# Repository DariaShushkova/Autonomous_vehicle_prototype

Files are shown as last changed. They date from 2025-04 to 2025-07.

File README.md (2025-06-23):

<div align="center">

Typing SVG (https://git.io/typing-svg)

Autonomous Driving System (**ADS**) is a **Line Following and Obstacle Avoiding Robot** built as semester project for **System Engineering & Prototyping** module at Hochschule Hamm-Lippstadt.

</div>

### Project Structure

1. Software For ADS
    - Directory: Autonomous Vehicle Code/
    - Contents: CodeOfTheSystem/, README.md
    - [Documenation](https://github.com/DariaShushkova/Autonomous_vehicle_prototype/tree/main/Autonomous%20Vehicle%20Code)

2. Datasheets for all Components
    - Directory: Hardware Datasheets/
    - Contents: Datasheets, README.md
    - [Documentation](https://github.com/DariaShushkova/Autonomous_vehicle_prototype/tree/main/Hardware%20Datasheets)

3. Mechanical Prototypes
    - Directory: Mechanical Prototype Design/
    - Contents: SolidWorks Parts, STL files for 3D printing, README.md
    - [Documentation](https://github.com/DariaShushkova/Autonomous_vehicle_prototype/tree/main/Mechanical%20Prototype%20Design)

4. Analysis and Visual Representation
    - Directory: Prototype Analysis/
    - Contents: Code Representation/, Visualization/
    - [Documentation](https://github.com/DariaShushkova/Autonomous_vehicle_prototype/tree/main/Prototype%20Analysis)

5. Simulated Circuitry
    - Directory: Simulation/
    - Contents: ArduinoCodeForDeployment/, Circuit Diagram & Setup
    - [Documenation](https://github.com/DariaShushkova/Autonomous_vehicle_prototype/tree/main/simulation)

6. Corrent and Voltage Measurement
    - Directory: CurrentAndVoltageMeasurement/
    - Contents: Images of voltage and current measurements for all components.
    - [Documentation](https://github.com/DariaShushkova/Autonomous_vehicle_prototype/tree/main/CurrentAndVoltageMeasurements)

7. Unit Testing
    - Directory: Software Testing
    - Contents: Unit_Tests/, all program files, Voltage Measurement Protocol.pdf
    - [Documentation](https://github.com/DariaShushkova/Autonomous_vehicle_prototype/tree/main/Software%20Testing)

### Competiton Recording
[Youtube](https://youtu.be/u-iqNwPsLXI)

### Components

1. chassis
2. DC Motors x2
3. IR Sensor x2
4. Ultrasonic Sensor x2
5. Motor Driver
6. Wheels
7. Color Sensor
8. Battery
9. Breadboard
10. Arduino

### Contributors

- [Daria Shushkova](https://github.com/DariaShushkova)
- [Andrey Sysoev](https://github.com/andrey-sysoev)
- [Mohamed Amer](https://github.com/amer195)
- [SamRB-dev](https://github.com/SamRB-dev)

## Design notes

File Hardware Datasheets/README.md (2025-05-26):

<div align="center">

Typing SVG (https://git.io/typing-svg)

</div>

### Overview

This directory contains the datasheets for every components used in the project.

### File Included

- Arduino Uno R4.pdf
- Color Sensor TCS3200.pdf
- Conrad LiPo Battery 3200mAh.pdf
- KY-033 IR Sensor.pdf
- Motor Driver L298N.pdf
- Ultrasonic Sensor HCSR04.pdf

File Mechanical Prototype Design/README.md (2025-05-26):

<div align="center">

Typing SVG (https://git.io/typing-svg)

</div>

### Overview

This part of the project contains 3D models for an Arduino-based autonomous vehicle prototype that will be used on the deployment stage.

### Directory Included

- [SolidWorks Parts](https://github.com/DariaShushkova/Autonomous_vehicle_prototype/tree/main/Mechanical%20Prototype%20Design/SolidWorks%20Parts) (Design files)
- [STL files](https://github.com/DariaShushkova/Autonomous_vehicle_prototype/tree/main/Mechanical%20Prototype%20Design/STL%20files) (For 3D printing)

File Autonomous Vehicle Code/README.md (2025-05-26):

<div align="center">

Typing SVG (https://git.io/typing-svg)

</div>

### Overview

This directory contains the code for the robot. The code consists of Motor control, robot navigation and ultrasonic sensor component. The motor control component (**MotorControl.h & MotorControl.cpp**) handles the states such as *leftSpeed, rightSpeed, leftForward, leftBackward, rightForward, rightBackward* and movement to different directions. The navigation component (**RobotNavigation.cpp & RobotNavigation.h**) handles obstacle detection, avoidance and movement based on the states of Motor controller. And lastly, the ultrasonic component (**UltrasonicSensor.h & UltrasonicSensor.cpp**) contains the code for ultrasonic sensor.

### File Included

1. Header Files
    - MotorControl.h
    - RobotNavigation.h
    - UltrasonicSensor.h
2. Program files
    - main.cpp
    - RobotNavigation.cpp
    - UltrasonicSenor.cpp

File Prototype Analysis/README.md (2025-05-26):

<div align="center">

Typing SVG (https://git.io/typing-svg)

</div>

### Overview

This directory contains the prototype analysis report in the form of code and visualization. The visualization contains the jpg files for various diagrams and the code contains html representation of the diagrams drawn in [Draw.io](https://draw.io).

### Directory Included

- [Code Representation](https://github.com/DariaShushkova/Autonomous_vehicle_prototype/tree/main/Prototype%20Analysis/Code%20Representation)
- [Visualization](https://github.com/DariaShushkova/Autonomous_vehicle_prototype/tree/main/Prototype%20Analysis/Visualization)

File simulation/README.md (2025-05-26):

<div align="center">

Typing SVG (https://git.io/typing-svg)

</div>

### Overview

This part of the project implements an Arduino-based autonomous vehicle prototype. The vehicle uses line detection and obstacle avoidance, including color-based object handling, to navigate predefined tracks. Supports routing variations like ovals, figure-eights, and parking maneuvers. Also contains the deployed code for the robot.

### Features

- Line tracking
- Obstacle detection and avoidance
- Color-based decision logic
- Speed optimization
- Supports various driving patterns (oval, figure-eight, parking)

### Simulation

The project is modeled and tested using Tinkercad.

[View Simulation](https://www.tinkercad.com/things/jz61uT7Gl9G-autonomous-vehicle-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)

### Files & Directory Included

- [ArduinoCodeForDeployment](https://github.com/DariaShushkova/Autonomous_vehicle_prototype/tree/main/simulation/ArduinoCodeForDeployment)
- AutonomousVehicleCode.cpp
- Circuit Diagram.pdf
- CircuitSetup.jpg

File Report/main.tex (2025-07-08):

\documentclass[conference]{IEEEtran}
\IEEEoverridecommandlockouts
\usepackage{comment}
\usepackage{cite}
\usepackage{amsmath,amssymb,amsfonts}
\usepackage{algorithmic}
\usepackage{graphicx}
\usepackage{textcomp}
\usepackage{xcolor}
\usepackage{hyperref}
\usepackage{listings}
\usepackage{float}
\usepackage{graphicx}
\usepackage{adjustbox}
\usepackage{enumitem}
\lstset{
  language=C++,
  basicstyle=\ttfamily\footnotesize,
  keywordstyle=\color{blue},
  commentstyle=\color{gray}\itshape,
  stringstyle=\color{red},
  numbers=none,
  numbersep=5pt,
  frame=single,
  breaklines=true,
  breakatwhitespace=true,
  postbreak=\mbox{\textcolor{gray}{$\hookrightarrow$}\space},
  showstringspaces=false,
  captionpos=b,
  tabsize=2
}

\def\BibTeX{{\rm B\kern-.05em{\sc i\kern-.025em b}\kern-.08em
    T\kern-.1667em\lower.7ex\hbox{E}\kern-.125emX}}

\begin{document}

\title{Design and Implementation of a Line Following and Obstacle Avoidance Robot}

\author{
\IEEEauthorblockN{Mohamed Amer\IEEEauthorrefmark{1}, Daria Shushkova\IEEEauthorrefmark{1},Andrey Sysoev\IEEEauthorrefmark{1}, Sadim Rahman\IEEEauthorrefmark{1}}
\IEEEauthorblockA{\IEEEauthorrefmark{1}Systems Engineering and Prototyping, BSc Electronic Engineering\\
Hochschule Hamm-Lippstadt, Lippstadt, Germany\\
\{mohamed-ahmed-mohamed-ali.amer, daria.shushkova, andrey.sysoev, sadim-rahman.badhan\}@stud.hshl.de}
}

\maketitle

%\begin{abstract}
%This paper presents the.
%\end{abstract}

%\begin{IEEEkeywords}
%Line follower robot,
%\end{IEEEkeywords}

\section{Introduction}
This project focuses on the development of a simple mobile robot that can autonomously follow a black line on a white surface and avoid obstacles placed in its path. The robot uses infrared sensors to detect the line and an ultrasonic sensor to detect nearby objects. An Arduino microcontroller is used to process sensor inputs and control motors accordingly.

\section{System Design and Engineering}
The robot design was developed based on \textbf{tasks} and \textbf{milestones} defined at the beginning of the project. These included line following, obstacle detection and avoidance, and integration of all components into a working prototype. It uses two infrared (IR) sensors to detect the black line and an ultrasonic sensor to measure the distance from obstacles. These sensors send signals to an Arduino Uno, that acts as the main controller.

The Arduino processes data and decides how the system should respond: either adjusting its path to stay on the line or stopping and maneuvering around an obstacle. Movement is handled by two DC motors controlled through an L298N motor driver.

Power is provided by a 9V battery pack, with regulation to supply the required voltages for the microcontroller and sensors. A simplified block diagram of the system is shown in Fig.~\ref{fig:block}

The vision of a system started with creating SysML diagrams to preserve and structure our project. It has the four Pillars of SysML:
\vspace{1em}
\begin{itemize}
  \item Requirements modeling (e.g., requirement diagram)
  \item Parametric modeling
  \item Structural modeling (e.g., Block Definition diagrams (BDD), Internal Block diagrams (IBD))
  \item Behavioral modeling (e.g., Use Case diagrams, Activity Diagrams, Sequence Diagrams, State Machine Diagrams)
\end{itemize}
\vspace{1em}
\begin{enumerate}

\item \textbf{Requirement Diagram}

 \hspace*{1em}It contains both \textbf{functional} and \textbf{nonfunctional} requirements of the autonomous vehicle system. These include navigation, obstacle handling, speed optimization, and route management,  with their derived requirements and hardware components.
 
 \hspace*{1em}See Fig~\ref{fig:req} the Requirement diagram.
 \vspace{1em}
\item \textbf{Parametric Diagram}

 \hspace*{1em}The \textbf{ Parametric Diagram} define parametric relationships between properties of blocks. This section uses parametric diagrams to represent mathematical and physical constraints of system behavior. See  Fig~\ref{fig:par} the Parametric diagram.
\vspace{1em}
\item \textbf{Block Definition Diagram}

\hspace*{1em}The \textbf{Block Definition Diagram (BDD)} provides a  structural decomposition of the \textit{Autonomous Vehicle System}. It represents the main logical blocks and how they are hierarchically related through composition relationships.

\vspace{1em}The  system is broken down into three primary subsystems:
\begin{itemize}
    \item \textbf{Chassis:} Includes physical mounting blocks such as the battery and breadboard holder, IR sensor holder, motor holder, and ultrasonic sensor holder.
    
    \item \textbf{Controllers:} Main controller (\textit{Arduino}) and the motor controller block responsible for driving the actuators.
    
    \item \textbf{Components:} Wheels and motors, which are part of the physical actuation system.
\end{itemize}
\hspace*{1em}See  Fig~\ref{fig:blockDef} the Block Definition diagram .

\item\textbf{Use Case Diagram}

Use case diagram models the interactions between \textbf{User} (the operator) and system functionalities. 
The diagram focuses on a \textit{"happy path"} — \textbf{Drive Autonomously}, which includes supporting behaviors like:

\begin{itemize}[nosep, left=0pt]
    \item Adjust Speed
    \item Avoid Obstacle
    \item Follow Path
\end{itemize}
\vspace{0.8em}
Extra behaviors such as \textbf{Drive in Oval} and \textbf{Drive in Figure Eight} are modeled as extensions of the routing logic.

\hspace*{1em}See  Fig~\ref{fig:use} the Use Case diagram.
\vspace{1em}
\item \textbf{State Machine Diagram}

The system begins in the "\textbf{stopped}" state. Upon initialization,it switches to the "\textbf{perform autonomous navigation}" state, where it drives left or right based on the input of the line-following sensor. If obstacle has been detected, system transitions to the "\textbf{obstacle\_avoid}" state. 
\hspace*{1em}In "\textbf{obstacle\_avoid}", the vehicle maneuvers around the obstacle:
\begin{itemize}
    \item it goes "\textbf{backward}" until save distance to do a maneuver
    \item chooses path depending if where are walls on the "\textbf{left}" or "\textbf{right}"
    \item  does "\textbf{line search}" to find the path after obstacle avoidance have been completed
\end{itemize}
\hspace*{1em}See  Fig~\ref{fig:state machine-diagram} the State Machine diagram.
\vspace{1em}
\item \textbf{Sequence Diagram}

\hspace*{1em}The \textbf{Sequence Diagram} shows the interaction between the Operator, AVS Controller, sensors, and motor control during autonomous navigation. The controller continuously uses path and obstacle data to send commands to motors: \texttt{setForward()}, \texttt{setLeft()}, or \texttt{setRight()}.

\hspace*{1em}If an obstacle is detected, the system enters \textbf{Obstacle Avoid Mode}, executing timed motor actions. An \texttt{alt} block handles conditional stopping or recovery based on search timeout and sensor feedback.

\hspace*{1em}See  Fig~\ref{fig:seq} the Sequence diagram.
\end{enumerate}
\vspace{1em}
\section{Prototyping and Design}
Our team was supplied with several Electronic components and a pre-designed chassis for development of the line follower vehicle. Our team was tasked to design a suitable mechanical design that would perform well in practice while utilizing all of the functionalities requested. A iterative design methodology was used to reach the final design made. 
\subsection{Electronic Components}
As shown in Table~\ref{tab:Electronic Components} a brief about the electronic components supplied and their purpose is mentioned. Key components that needed much attention were the infrared sensor, the battery and the motor driver. The Infrared sensor was a digital active high sensor.Thus, it was needed to be calibrated on the line we are following. Furthermore, dealing with the battery and the motor driver supplied, it was critical to ensure that voltages coming out of the motor driver voltage regulator are 5 volts. otherwise, this will expose the components to permanent damage. For safety purposes and avoiding any damaging to the components, we simulated the entire circuit in TinkerCad \cite{tinkercad}.

\subsection{Virtual and Physical Prototypes}
All of the prototyping design iterations were simulated in Solid works software. Our goal was to design as few parts as we can to avoid the given printing time limit. It was agreed on at the end to use the following parts followed by their main objective: \begin{itemize}
    \item \textbf{2x Motor mounts:} The motor mounts were used to mount the motors in a rigid way so it can support the entire weight of the vehicle.
     \item \textbf{2x IR sensor mounts:} The main objective is to keep the IR sensors too close to the ground to avoid lighting noise from the surrounding environment
      \item \textbf{2x Ultrasonic mounts:} Really lightweight components just to fix the ultrasonic without causing a high penality in printing time
       \item \textbf{battery and breadboard mount:} It function is to be multifunctional part holding the breadboard on its upper side and securing the battery underneath it
\end{itemize} 
Our first print trial was not so successful at the beginning due to unaccounted error in our design. Then the parts were modified to have some fit tolerance to account for the error resulting from the 3D printer. Moreover on design iterations, we included slots instead of holes for the IR sensors so their position can be easily modified if needed. A visualization of the final prototype reached is shown in Figure~\ref{fig:prototype}.
\begin{figure}[H]
    \centering
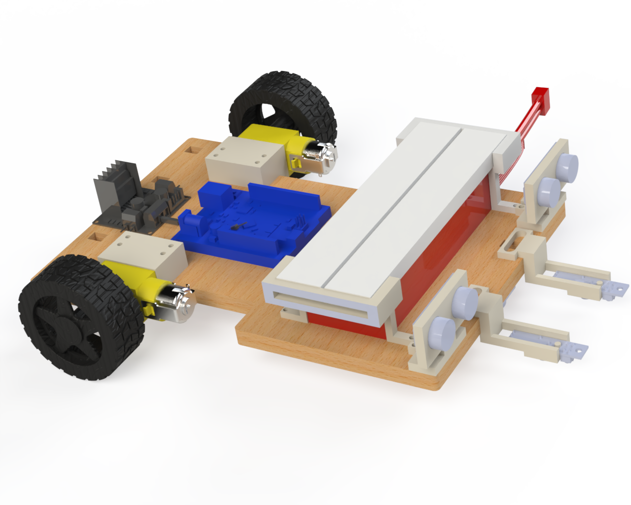
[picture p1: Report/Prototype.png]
    
    \caption{Block diagram of the line following and obstacle avoidance robot.}
    \label{fig:prototype}
\end{figure}

\subsection{Hardware Assembly}
All components were mounted on a chassis and connected as per the schematic. For assembly, all of the parts were mounted using spax screws in 3 different lengths : 10mm, 16mm, 20mm with all of them being M3 diameter. Some holes in the wooden chassis were done using a drill. All of the components were mounted without any adhesive materials. In our assembly, it was made sure that all components were firmly secured in position. 

\section{Circuit Design}
%\begin{itemize}
 %   \item The schematic includes sensors, motor driver, Arduino, and power source.
  %  \item Wiring includes proper voltage connections and pin mappings for sensors and motors.
%\end{itemize}

The autonomous vehicle circuit integrates multiple sensor and actuator subsystems using an Arduino Uno as the main controller. The complete circuit layout simulation in tinkercad is shown in Fig.~\ref{fig:CircuitSetup}.

The wiring was designed to fulfill three key goals: modularity, robustness, and safe power distribution. Each subsystem was treated as an independent module, allowing for easier debugging and incremental development.

\subsection{Sensor Integration}
\begin{itemize}
  \item \textbf{Infrared Line Sensors (2x)} are connected to digital input pins D12 and D13. These sensors detect the black line against the white surface, and their values are read in real-time to determine the robot's lateral alignment.

  \item \textbf{Ultrasonic Sensors (2x)} are mounted on the front-left and front-right sides. Their trigger and echo pins are connected to D6/D7 (right) and D8/D9 (left). These provide real-time distance feedback to avoid collisions.

  \item \textbf{Color Sensor (1x)} is connected to analog pins A0 to A4. It adds redundancy to object classification, allowing the robot to treat red-colored obstacles differently (e.g., push or bypass).
\end{itemize}

\subsection{Actuator Wiring}
The circuit schematic of the Motor Driver along with the motors and ultrasonic sensors is shown in ~\ref{fig:Schematic}.
\begin{itemize}
  \item \textbf{Motor Driver (L298N)} is used to control two DC motors. It is connected to:
  \begin{itemize}
    \item PWM pins D10 and D11 for speed control
    \item Direction control pins D2–D5
  \end{itemize}
  The motors are powered directly from the 12V battery pack via the motor driver's onboard regulator.
\end{itemize}

\subsection{Power Management}
\begin{itemize}
  \item A 12V DC battery pack supplies power to both motors and the Arduino.
  \item A voltage regulator onboard the L298N downscales the 12V to 5V for the Arduino and sensors, avoiding voltage spikes and protecting delicate components.
  \item Decoupling capacitors are placed across power lines to minimize electrical noise and ensure stable analog sensor readings.
\end{itemize}

\subsection{Pin Mapping Overview}
The Table ~\ref{tab:pinmap} shows the pins that were used in details.
\begin{table}[H]
\centering
\caption{Key Pin Assignments}
\label{tab:pinmap}
\begin{tabular}{|l|l|}
\hline
\textbf{Component} & \textbf{Pin(s)} \\ \hline
IR Sensor (Left) & D13 \\ \hline
IR Sensor (Right) & D12 \\ \hline
Ultrasonic Sensor (Left) & D8 (Trig), D9 (Echo) \\ \hline
Ultrasonic Sensor (Right) & D6 (Trig), D7 (Echo) \\ \hline
Left Motor & D2 (F), D3 (B), D10 (PWM) \\ \hline
Right Motor & D4 (F), D5 (B), D11 (PWM) \\ \hline
Color Sensor & A0–A4 \\ \hline
\end{tabular}
\end{table}

\subsection{Schematic Analysis}
The circuit was simulated and verified using Tinkercad and real-world breadboard prototyping. Care was taken to route ground lines properly, avoid floating inputs, and apply pull-down resistors where needed.

The design emphasizes modularity, with all sensors and motors detachable via male/female header connectors for ease of maintenance and reassembly.

\section{Software Implementation}
\label{soft}

\subsection{Initialization of Sensors and Actuators}
\subsubsection*{\textbf{1. Sensors Initialization}}

\begin{enumerate}[label=\alph*)]

\item \textbf{Ultrasonic Sensors (Left/Right)} — Pins for the ultrasonic sensors are defined in the file 'UltrasonicSensor.h'. They are set up and initialized in the 'UltrasonicSensor.cpp' and 'main.cpp' files. Relevant snippets are shown below:

\begin{lstlisting}[language=C++, caption=Pin definitions in UltrasonicSensor.h]
// Ultrasonic sensor pin definitions
#define LEFT_TRIG_PIN 8
#define LEFT_ECHO_PIN 9
#define RIGHT_TRIG_PIN 6
#define RIGHT_ECHO_PIN 7
\end{lstlisting}

\begin{lstlisting}[language=C++, caption=Pin setup in UltrasonicSensor.cpp]
// Set trigger as output and echo as input
void UltrasonicSensor::begin() {
   pinMode(trigPin, OUTPUT);
   pinMode(echoPin, INPUT);
}
\end{lstlisting}

\begin{lstlisting}[language=C++, caption=Sensor initialization in main.cpp]
// Create hardware instances
...
UltrasonicSensor rightUltrasonic(
  RIGHT_TRIG_PIN,
  RIGHT_ECHO_PIN);
UltrasonicSensor leftUltrasonic(
  LEFT_TRIG_PIN,
  LEFT_ECHO_PIN);
RobotNavigation robotNav(
  &rightUltrasonic,
  &leftUltrasonic,
  &motor);
 
// Initialize ultrasonic sensors
void setup() {
   ...
   rightUltrasonic.begin();
   leftUltrasonic.begin();
   ...
}
\end{lstlisting}

\item \textbf{IR Sensors (Left/Right)} — Pins for the IR sensors are defined in 'RobotNavigation.h' and initialized in 'RobotNavigation.cpp' and in 'main.cpp'. Relevant snippets are shown below:

\begin{lstlisting}[language=C++, caption=IR sensor pin definitions in RobotNavigation.h]
// Line sensor digital pins
#define LINE_SENSOR_LEFT 13
#define LINE_SENSOR_RIGHT 12
\end{lstlisting}

\begin{lstlisting}[language=C++, caption=IR sensor pin initialization in RobotNavigation.cpp]
void RobotNavigation::begin() {
  pinMode(LINE_SENSOR_LEFT, INPUT);
  pinMode(LINE_SENSOR_RIGHT, INPUT);
}
\end{lstlisting}

\begin{lstlisting}[language=C++, caption=IR sensor pin initialization in main.cpp]
void setup() {
  ...
  // Start navigation system
  robotNav.begin();
}
\end{lstlisting}

\item \textbf{Color Sensor} — Pins for the color sensor are defined in 'ColorSensor.h' and initialized in 'ColorSensor.cpp'. Relevant snippets are shown below:

\begin{lstlisting}[language=C++, caption=Color sensor pin definitions in ColorSensor.h]
// Pin definitions
#define COLOR_SENSOR_OUTPUT_FREQUENCY_INPUT_S0 A0
#define COLOR_SENSOR_OUTPUT_FREQUENCY_INPUT_S1 A1
#define COLOR_SENSOR_PHOTODIODE_INPUT_S2 A2
#define COLOR_SENSOR_PHOTODIODE_INPUT_S3 A3
#define COLOR_SENSOR_OUTPUT_PIN A4
\end{lstlisting}

\begin{lstlisting}[language=C++, caption=Color sensor pin initialization in ColorSensor.cpp]
void ColorSensor::ColorSensorInit() {
    pinMode(
      COLOR_SENSOR_OUTPUT_FREQUENCY_INPUT_S0,
      OUTPUT);
    pinMode(
      COLOR_SENSOR_OUTPUT_FREQUENCY_INPUT_S1,
      OUTPUT);
    pinMode(
      COLOR_SENSOR_PHOTODIODE_INPUT_S2,
      OUTPUT);
    pinMode(
      COLOR_SENSOR_PHOTODIODE_INPUT_S3,
      OUTPUT);
    pinMode(
      COLOR_SENSOR_OUTPUT_PIN,
      INPUT);

    digitalWrite(
      COLOR_SENSOR_OUTPUT_FREQUENCY_INPUT_S0,
      HIGH); // Full scale
    digitalWrite(
      COLOR_SENSOR_OUTPUT_FREQUENCY_INPUT_S1,
      LOW); // Frequency scaling = 20%
}
\end{lstlisting}
\end{enumerate}

\subsubsection*{\textbf{2. Actuators (Motors) Initialization}}
Motor Control Pins are defined in the file 'MotorControl.h'. Their setup and initialization are made in the 'main.cpp' file. Relevant snippets are shown below:

\begin{lstlisting}[language=C++, caption=Pin definitions in MotorControl.h]
// Motor control pin definitions
#define LEFT_MOTOR_SPEED_PIN 10
#define RIGHT_MOTOR_SPEED_PIN 11
#define LEFT_MOTOR_FORWARD_PIN 2
#define LEFT_MOTOR_BACKWARD_PIN 3
#define RIGHT_MOTOR_FORWARD_PIN 4
#define RIGHT_MOTOR_BACKWARD_PIN 5
\end{lstlisting}

\begin{lstlisting}[language=C++, caption=Pins initialization in main.cpp]
// Create hardware instances
MotorControl motor;
...

RobotNavigation robotNav(
  &rightUltrasonic,
  &leftUltrasonic,
  &motor
);
// Arduino initialization
void setup() {
  // Setup motor pins as outputs
  pinMode(LEFT_MOTOR_SPEED_PIN, OUTPUT);
  pinMode(RIGHT_MOTOR_SPEED_PIN, OUTPUT);
  pinMode(LEFT_MOTOR_FORWARD_PIN, OUTPUT);
  pinMode(LEFT_MOTOR_BACKWARD_PIN, OUTPUT);
  pinMode(RIGHT_MOTOR_FORWARD_PIN, OUTPUT);
  pinMode(RIGHT_MOTOR_BACKWARD_PIN, OUTPUT);
  ...
}
\end{lstlisting}

\subsubsection*{Key Initialization Features}
\begin{enumerate}
  \item \textbf{Pin Abstraction}
    \begin{itemize}
      \item Hardware pins are abstracted via \verb|#define| macros.
      \item Logical separation of sensor and actuator types.
    \end{itemize}
  \item \textbf{Modular Initialization}
    \begin{itemize}
      \item Each sensor type has its own initialization routine.
      \item Motor control setup is centralized in \texttt{main.cpp}.
    \end{itemize}
  \item \textbf{Hardware–Software Mapping}
    \begin{itemize}
      \item On Fig.~\ref{fig:block}, the block diagram shows how each hardware component is mapped to specific software-controlled pins in the Arduino controller.
    \end{itemize}
\end{enumerate}

This summary ensures the reader understands the overarching design—pin abstraction, modular setup, mapping, and your carefully ordered startup sequence—before diving into higher‑level behavior logic.

\subsection{Movement Control Algorithms}

\subsubsection*{\textbf{1. Core Movement Methods}}

\begin{enumerate}[label=\alph*)]

\item \textbf{Forward and Backward Motion} - The robot’s linear motion is achieved through symmetric control of both motors using Pulse Width Modulation (PWM) for speed regulation. The direction of rotation is set by toggling the appropriate H-bridge control pins. The methods of the \texttt{MotorControl class} in 'MotorControl.cpp' show the implementation of forward and reverse movement:

\begin{lstlisting}[language=C++, caption=Forward and backward movement functions]
// Move robot straight forward at given speed
void MotorControl::moveForward(int speed) {
  analogWrite(LEFT_MOTOR_SPEED_PIN, speed);
  analogWrite(RIGHT_MOTOR_SPEED_PIN, speed);
  digitalWrite(LEFT_MOTOR_FORWARD_PIN, LOW);
  digitalWrite(LEFT_MOTOR_BACKWARD_PIN, HIGH);
  digitalWrite(RIGHT_MOTOR_FORWARD_PIN, LOW);
  digitalWrite(RIGHT_MOTOR_BACKWARD_PIN, HIGH);
}

// Move robot straight backward at given speed
void MotorControl::moveBackward(int speed) {
  analogWrite(LEFT_MOTOR_SPEED_PIN, speed);
  analogWrite(RIGHT_MOTOR_SPEED_PIN, speed);
  digitalWrite(LEFT_MOTOR_FORWARD_PIN, HIGH);
  digitalWrite(LEFT_MOTOR_BACKWARD_PIN, LOW);
  digitalWrite(RIGHT_MOTOR_FORWARD_PIN, HIGH);
  digitalWrite(RIGHT_MOTOR_BACKWARD_PIN, LOW);
}
\end{lstlisting}

\textbf{Key Algorithm:}
\begin{itemize}
  \item PWM signals regulate motor speed via \verb|analogWrite()|.
  \item H-bridge circuits manage direction through digital pins.
  \item Equal PWM ensures coordinated, straight-line movement.
\end{itemize}

\item \textbf{Pivotal Turning} - For medium-radius turns, one motor is activated while the other is disabled, allowing the robot to pivot around the unpowered wheel. The \verb|turnLeft()| and \verb|turnRight()| methods implement this by powering one motor while setting both control pins for the other motor to \verb|LOW|, causing it to freewheel or coast. This creates a smoother turn compared to a point rotation.

\begin{lstlisting}[language=C++, caption=Single-wheel pivot turn functions]
// Turn robot to the left
void MotorControl::turnLeft(int speed) {
  analogWrite(LEFT_MOTOR_SPEED_PIN, speed);
  digitalWrite(LEFT_MOTOR_FORWARD_PIN, LOW);
  digitalWrite(LEFT_MOTOR_BACKWARD_PIN, HIGH);
  digitalWrite(RIGHT_MOTOR_FORWARD_PIN, LOW);
  digitalWrite(RIGHT_MOTOR_BACKWARD_PIN, LOW);
}

// Turn robot to the right
void MotorControl::turnRight(int speed) {
  analogWrite(RIGHT_MOTOR_SPEED_PIN, speed);
  digitalWrite(LEFT_MOTOR_FORWARD_PIN, LOW);
  digitalWrite(LEFT_MOTOR_BACKWARD_PIN, LOW);
  digitalWrite(RIGHT_MOTOR_FORWARD_PIN, LOW);
  digitalWrite(RIGHT_MOTOR_BACKWARD_PIN, HIGH);
}

\end{lstlisting}

\textbf{Key Algorithm:}
\begin{itemize}
    \item Only one motor is actively powered for the turn.
    \item The other motor is disabled and its wheel is allowed to coast, serving as the pivot point.
    \item The turning radius is determined by the robot's geometry and the speed of the powered wheel.
\end{itemize}

\item \textbf{In-Place Rotation} - In-place rotation is accomplished by driving both motors in opposite directions at equal speed. This results in a zero turning radius, allowing the robot to pivot around its center. The technique is useful in constrained environments or for rapid heading adjustments.

\begin{lstlisting}[language=C++, caption=Counter-rotational in-place turning]
// Rotate robot to the right
void MotorControl::rotateRight(int speed) {
  analogWrite(RIGHT_MOTOR_SPEED_PIN, speed);
  analogWrite(LEFT_MOTOR_SPEED_PIN, speed);
  digitalWrite(LEFT_MOTOR_FORWARD_PIN, HIGH);
  digitalWrite(LEFT_MOTOR_BACKWARD_PIN, LOW);
  digitalWrite(RIGHT_MOTOR_FORWARD_PIN, LOW);
  digitalWrite(RIGHT_MOTOR_BACKWARD_PIN, HIGH);
}

// Rotate robot to the left
void MotorControl::rotateLeft(int speed) {
  analogWrite(RIGHT_MOTOR_SPEED_PIN, speed);
  analogWrite(LEFT_MOTOR_SPEED_PIN, speed);
  digitalWrite(LEFT_MOTOR_FORWARD_PIN, LOW);
  digitalWrite(LEFT_MOTOR_BACKWARD_PIN, HIGH);
  digitalWrite(RIGHT_MOTOR_FORWARD_PIN, HIGH);
  digitalWrite(RIGHT_MOTOR_BACKWARD_PIN, LOW);
}

\end{lstlisting}

\textbf{Key Algorithm:}
\begin{itemize}
  \item Opposite motor directions produce a central rotation.
  \item Equal PWM ensures balanced torque and pivoting.
  \item Enables highly responsive directional changes.
\end{itemize}

\item \textbf{Stopping Mechanism} - To halt motion, both motors are actively short-braked by setting both control lines to \verb|HIGH|. Simultaneously, PWM is set to its maximum to ensure full coil engagement. This braking approach ensures faster and more stable stops compared to passive coasting.

\begin{lstlisting}[language=C++, caption=Active braking mechanism]
// Stop robot
void MotorControl::stopMotors() {
  analogWrite(LEFT_MOTOR_SPEED_PIN, 255);
  analogWrite(RIGHT_MOTOR_SPEED_PIN, 255);
  digitalWrite(LEFT_MOTOR_FORWARD_PIN, HIGH);
  digitalWrite(LEFT_MOTOR_BACKWARD_PIN, HIGH);
  digitalWrite(RIGHT_MOTOR_FORWARD_PIN, HIGH);
  digitalWrite(RIGHT_MOTOR_BACKWARD_PIN, HIGH);
}
\end{lstlisting}

\textbf{Key Algorithm:}
\begin{itemize}
  \item Short-circuit braking is applied to both motors.
  \item Ensures rapid deceleration and positional stability.
  \item Full PWM maximizes current for immediate response.
\end{itemize}
\end{enumerate}

\subsubsection*{\textbf{2. Parameterization and Tuning}}

To balance power consumption, control responsiveness, and maneuverability, a set of predefined constants are used for speed tuning. These constants are defined in the header file \texttt{RobotNavigation.h} and used throughout the motion control routines.

\begin{lstlisting}[language=C++, caption=Speed tuning parameters]
// Speed configurations
#define DefaultTurnSpeed 140   
#define DefaultRotateSpeed 120 
#define DefaultForwardSpeed 120 
#define DefaultBackwardSpeed 80
\end{lstlisting}

\textbf{Tuning Principles:}
\begin{itemize}
    \item \textbf{High Turn Speed:} The turning speed (140) is set higher than the forward speed to ensure rapid and responsive correction when the robot deviates from the line.
    \item \textbf{Controlled Rotation and Forward Motion:} Forward and rotation speeds (120) are balanced to provide stable movement during standard navigation and obstacle avoidance maneuvers.
    \item \textbf{Reduced Reverse Speed:} Reverse motion uses a lower PWM value (80) for increased precision and safety, particularly when backing away from an obstacle.
    \item \textbf{PWM Range:} All values are calibrated within the 0--255 PWM range to prevent motor saturation while providing adequate torque.
\end{itemize}

\subsubsection*{\textbf{3. Real-World Execution Flow}}

The robot's low-level movement primitives are integrated with sensor feedback to execute complex, high-level behaviors. The obstacle avoidance routine is a key example, combining multiple motion types in a timed and sensor-driven sequence.

\begin{lstlisting}[language=C++, caption=Excerpt from the Obstacle Avoidance Sequence]
// Behavior for obstacle avoidance sequence
void RobotNavigation::handleObstacleAvoidance() {
  switch (obstacleStep) {
    // Move backward to clear way for maneuver
    case 0:
      motor->stopMotors();
      delay(100);
      motor->moveBackward(DefaultBackwardSpeed);
      delay(200);
      obstacleStep++;
      break;
    // Rotate left before bypass
    case 1:
      motor->rotateLeft(80);
      delay(600);
      motor->stopMotors();
      delay(1000);
      obstacleStep++;
      break;
  } 
  
  // Check obstacle on the left side
  float rightDistance = rightSensor->getDistance();
  float leftDistance = leftSensor->getDistance();

  // Scenario 1: Obstacle detected 
  if ((rightDistance < 100 && rightDistance > 3) ||
      (leftDistance < 100 && leftDistance > 3)) {
      
    /* Rotate right to recover straight position.
    The while loop allows to find line back by
    rotating right until line is detected again */
    
    motor->rotateRight(68);
    while (true) {
      bool leftLine = digitalRead(LINE_SENSOR_LEFT);
      bool rightLine = digitalRead(LINE_SENSOR_RIGHT);
      if (rightLine == HIGH) {
        motor->stopMotors();
        delay(500);
        break;
      }
    }
    
    /* Once recovered the straight position, 
    rotate right to bypass from the right side 
    which is clear from obstacles */
    
    motor->rotateRight(75);
    delay(500);
    
    /* Bypass the obstacle by executing a pre-tuned 
    multi-step maneuver, developed through testing 
    with the specific hardware and environment 
    conditions */

  // Scenario 2: Obstacle is not detected 
  } else {
  
    // Rotate slightly right
    motor->rotateRight(75);
    delay(350);
    
    /* Execute bypass with pre-tuned multi-step 
    maneuver, developed through testing */
  }
  
  /* In the end of bypass, switch to 
  LINE_SEARCH to reacquire the path */
  currentState = LINE_SEARCH;
  setRobotState(LINE_SEARCH);
}
\end{lstlisting}

This procedure shows how low-level primitives (\texttt{moveBackward}, \texttt{rotateLeft}, etc.) are composed into a stateful, adaptive sequence. By layering control logic over robust actuator routines, the system achieves both predictability and adaptability in dynamic environments.

\subsection{Behavioral Decision Logic}

The robot's autonomy is governed by a state machine architecture implemented in the \texttt{RobotNavigation class}. This design ensures that the robot transitions between well-defined behaviors based on sensor inputs. The logic is visualized in the state machine diagram in Fig~\ref{fig:state machine-diagram} and implemented in the methods below.

\subsubsection*{\textbf{1. State Machine Architecture}}

The core of the decision-making process is located in the \texttt{updateNavigation()} method in 'RobotNavigation.cpp', which runs continuously. It performs the reading of all relevant sensors and the usage of a prioritized decision tree to select the robot's next state.

\begin{enumerate}[label=\alph*)]

\item \textbf{Core States} - The primary operational states are defined as macros in 'RobotNavigation.h'.
\begin{lstlisting}[language=C++, caption=State Definitions in RobotNavigation.h]
// Robot states
#define OBSTACLE_AVOID 0
#define LEFT 1
#define RIGHT 2
#define LINE_SEARCH 3
\end{lstlisting}

\item \textbf{State Transition Logic} - The state transition logic is based on a priority-based sequence implemented in the \texttt{updateNavigation()} method, where the obstacle avoidance is the highest priority.

\begin{lstlisting}[language=C++, caption=Decision Logic in RobotNavigation.cpp]
void RobotNavigation::updateNavigation() {
  // Read line and obstacle sensors
  int leftLine = digitalRead(LINE_SENSOR_LEFT);
  int rightLine = digitalRead(LINE_SENSOR_RIGHT);
  float rightDistance = rightSensor->getDistance();
  float leftDistance = leftSensor->getDistance();

  // Decision Tree
  // Priority 1: Obstacle detection
  if (((rightDistance < maxDistance &&
        rightDistance > minDistance) ||
      (leftDistance < maxDistance &&
       leftDistance > minDistance)) &&
      !red->ColorSensorObserve()) {
    motor->stopMotors();
    delay(300);
    setRobotState(OBSTACLE_AVOID); 
  }
  
  // Priority 2: Line following 
  
  // Right sensor lost the line
  if (leftLine == HIGH && rightLine == LOW) {
    motor->stopMotors();
    setRobotState(LEFT);  // Turn left
    
  // Left sensor lost the line 
  } else if (leftLine == LOW && rightLine == HIGH) {
    motor->stopMotors();
    setRobotState(RIGHT);  // Turn right
    
  // Both sensors lost the line 
  } else if (leftLine == LOW && rightLine == LOW) {
    // Invert last state  
    if (currentState == LEFT) {
      motor->stopMotors();
      setRobotState(RIGHT);
    } else if (currentState == RIGHT) {
      motor->stopMotors();
      setRobotState(LEFT);
    }
  }
}
\end{lstlisting}

An important feature of the decision logic is the integration of the color sensor. The robot should only enter the \texttt{OBSTACLE\_AVOID} state if the detected object is \texttt{NOT RED}, allowing it to push red objects off the line and continue following it.

\end{enumerate}

\subsubsection*{\textbf{2. State-Specific Behaviors}}

Once a state is set via \texttt{setRobotState()} method, a specific handler function is executed.

\begin{enumerate}[label=\alph*)]

\item \textbf{OBSTACLE\_AVOID State} — This is a multi-step routine managed by the \texttt{obstacleStep} attribute of the \texttt{RobotNavigate} class. It does not execute in a single function call but progresses through a sequence.

\begin{itemize}
    \item \textbf{Step 0 \& 1:} The robot first moves backward to create space, then rotates to face a new heading.
    \item \textbf{Conditional Bypass:} After the initial turn, the robot re-checks for another obstacle on the left. If one is detected within a 3-100 cm range, a longer, more complex bypass maneuver is executed: the robot first rotates right to recover its original position using the line sensors, and then rotates right again to initiate a bypass from the opposite side, which is presumed clear. Otherwise, a shorter maneuver is performed to return to the path (see Fig.~\ref{fig:state machine-diagram} and the code snippet in Listing 16)

    \item \textbf{Exit Condition:} Upon completing the bypass maneuver, the robot transitions to the \texttt{LINE\_SEARCH} state to reacquire the line.
\end{itemize}

\item \textbf{LEFT and RIGHT States} — These states handle the line-following course. The robot executes a pivot turn until the opposite sensor rediscovers the line, ensuring the robot straightens out. This logic applies a zig-zag pattern, allowing the robot to follow the line even through the sharpest curves.

\begin{lstlisting}[language=C++, caption=Line Correction Logic]
case LEFT:
  /* Turn left until the right IR sensor 
  detects the line */
  
  while (digitalRead(LINE_SENSOR_RIGHT) == LOW)
      motor->turnLeft(DefaultTurnSpeed); 
  motor->stopMotors();
  break;
  
case RIGHT: // The RIGHT case is symmetric
...
\end{lstlisting}

\item \textbf{LINE\_SEARCH State} — This state is triggered after the robot completes an obstacle avoidance maneuver. The logic of this state is implemented in the \texttt{handleLineSearch()} method in 'RobotNavigation.cpp'. The method executes a zig-zag pattern, first turning left and then right in small increments, until one of the sensors finds the line.

\begin{itemize}
    \item \textbf{Timeout Failsafe:} This search is constrained by a \texttt{searchTimeout} of 100,000 ms. If the line is not found within this period, the routine terminates, which corresponds to the transition to the final \texttt{STOPPED} state in the state diagram (see Fig.~\ref{fig:state machine-diagram}).
    \item \textbf{Re-alignment:} Once the line is detected, a final adjustment is made to center the robot before resuming forward motion.
\end{itemize}

\end{enumerate}

\begin{lstlisting}[language=C++, caption=Excerpt from the Line Search Sequence]
void RobotNavigation::handleLineSearch() {
  bool foundLine = false;
  unsigned long startTime = millis();
  while (millis() - startTime < searchTimeout) {
    motor->turnLeft(120);
    delay(110);
    motor->stopMotors();
    delay(100);

    bool leftLine = digitalRead(LINE_SENSOR_LEFT);
    bool rightLine = digitalRead(LINE_SENSOR_RIGHT);

    if (leftLine == HIGH || rightLine == HIGH) {
        // Realignment sequence
        if (leftLine == HIGH)
            while (rightLine == HIGH)
                motor->turnLeft(DefaultTurnSpeed);

        if (rightLine == HIGH)
            while (leftLine == HIGH)
                motor->turnRight(DefaultTurnSpeed);

        break;
    }

    // Try right turn if line not found and repeat
    motor->turnRight(DefaultTurnSpeed);
    delay(100);
    motor->stopMotors();
    delay(100);
    ...
}
\end{lstlisting}

\subsubsection*{\textbf{3. Behavioral Characteristics Summary}}

The Table~\ref{tab:behavior} summarizes the primary state transitions. The "Default" behavior of moving forward is the implicit action when no other trigger condition is met.

\section{Git Usage and Collaboration}
Project development was tracked using GitHub. In Table ~\ref{table:commit} ,The contributions of each member is shown according to the GitHub repository commits. The table can be found in the appendix.

\section{Key Achievements}
The initial state machine was simulated in UPPAAL in Figure ~\ref{fig:UPPAAL} flawlessly. Moreover, our autonomous car was able to follow the line smoothly, handling sharp turn at high speeds, successfully detecting obstacles and avoiding them, all of this while keeping a good accuracy of the line tracking. Moreover, we were successful in achieving successful integration of the hardware, consistency of results across multiple tests, effective collaboration using Git for version control and systematic testing and debugging approach.

\section*{Acknowledgment}

\begin{thebibliography}{00}
\bibitem{arduino} Arduino Documentation. \url{https://www.arduino.cc/en/Guide}
\bibitem{tinkercad} Tinkercad Simulation. \url{https://www.tinkercad.com}
\bibitem{uppaal} Uppaal Model Checker. \url{http://www.uppaal.org/}
\end{thebibliography}

\section*{Declaration of Originality}
We hereby declare that this report is our own work and that we have acknowledged all sources used.

\begin{center}
\appendix
\section*{Figures and Tables}
\end{center}

\begin{table}[h]
\centering
\begin{tabular}{l|c}
\hline
\textbf{Team Member} & \textbf{Number of Commits} \\
\hline
Mohamed Amer   & 30 \\
Daria Shushkova     & 72 \\
Andrey Sysoev    & 58  \\
Sadim Rahman     & 34  \\
\hline
\textbf{Total} & \textbf{194} \\
\hline
\end{tabular}
\vspace{1em}
\caption{GitHub Commits by Team Members}
\label{table:commit}
\end{table}

\begin{figure}[H]
    \centering
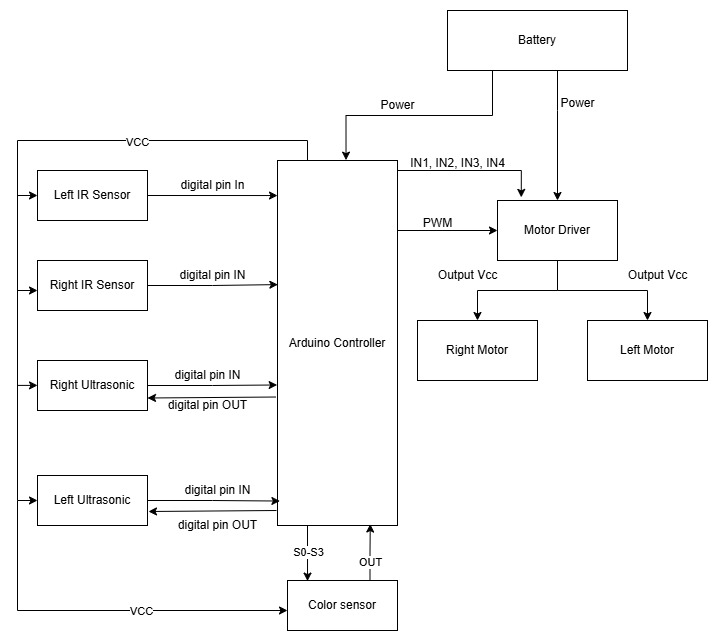
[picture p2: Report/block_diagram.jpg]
    
    \caption{Block diagram of the robot system architecture.}
    \label{fig:block}
\end{figure}
\clearpage
\begin{figure}[H]
    \centering
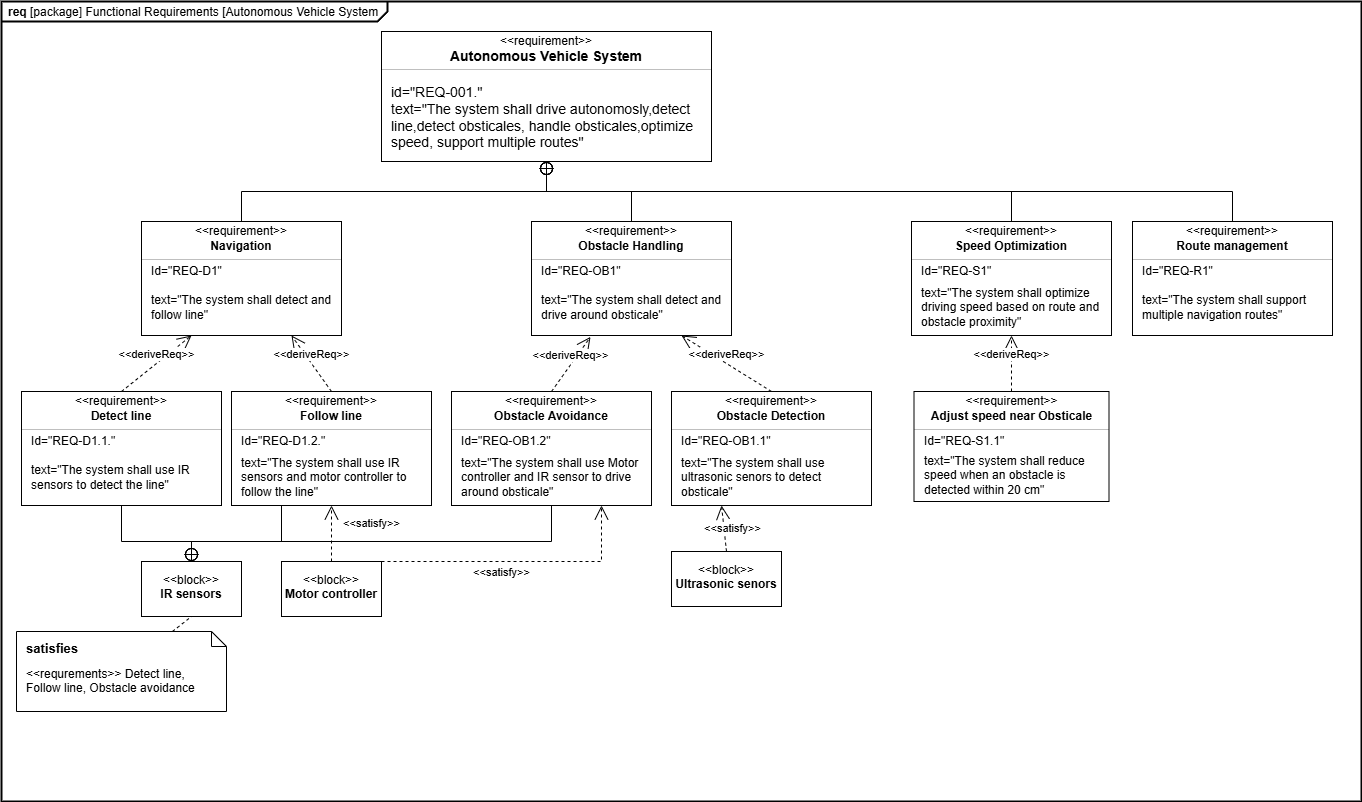
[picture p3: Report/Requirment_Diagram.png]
    
    \caption{Requirement diagram}
    \label{fig:req}
\end{figure}
\clearpage
 \begin{figure}[H]
    \centering
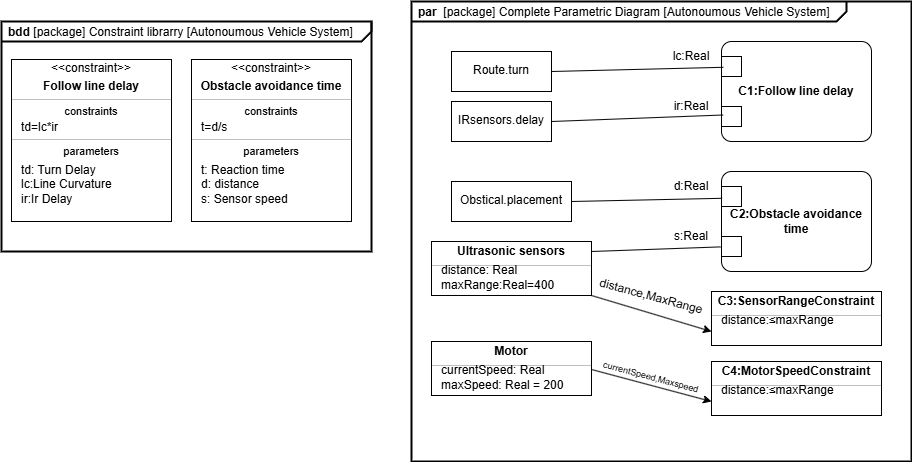
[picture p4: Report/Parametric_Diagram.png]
    
    \caption{Parametric diagram}
    \label{fig:par}
\end{figure}
\clearpage

\begin{figure}[H]
    \centering
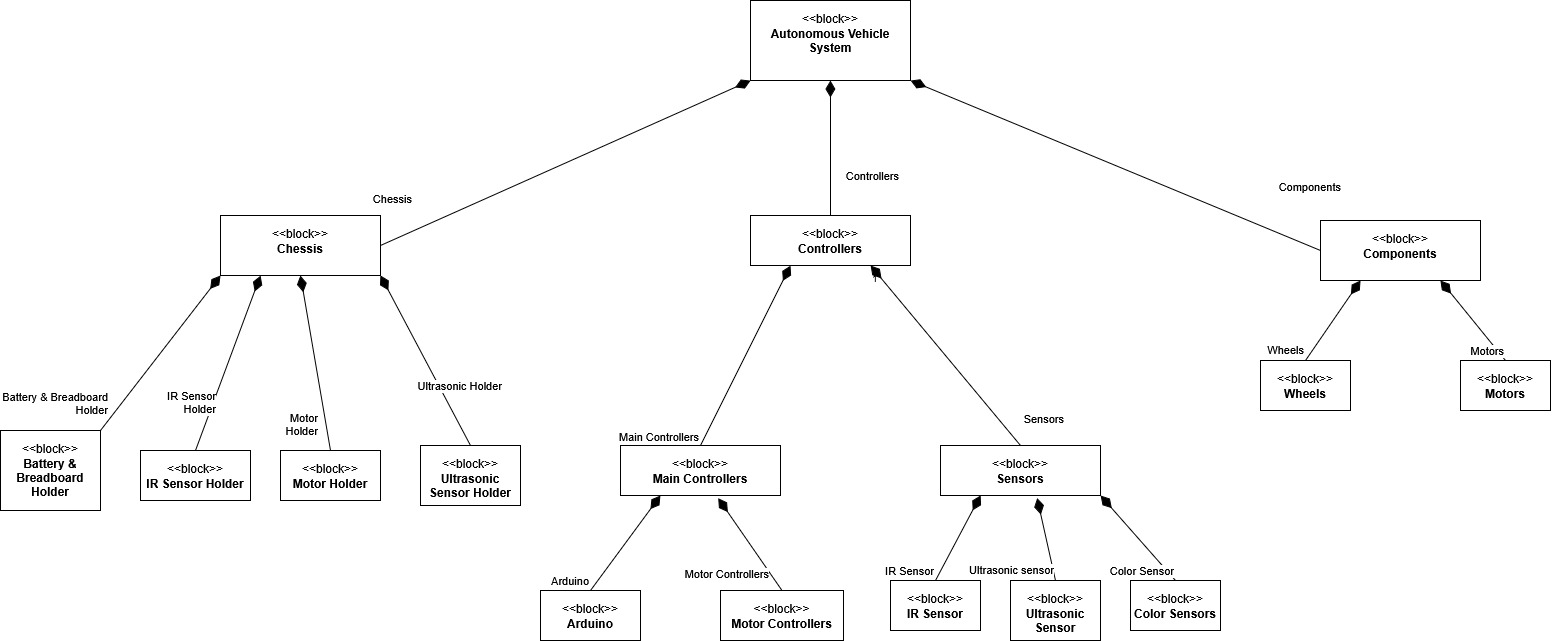
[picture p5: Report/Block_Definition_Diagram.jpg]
    
    \caption{Block Definition diagram}
    \label{fig:blockDef}
\end{figure}
\begin{figure}[H]
    \centering
    \includegraphics[width=1\textwidth]
    {UseCaseDiagram.png}
    \caption{Use Case diagram}
    \label{fig:use}
\end{figure}
\clearpage

    \begin{figure}[H]
    \centering
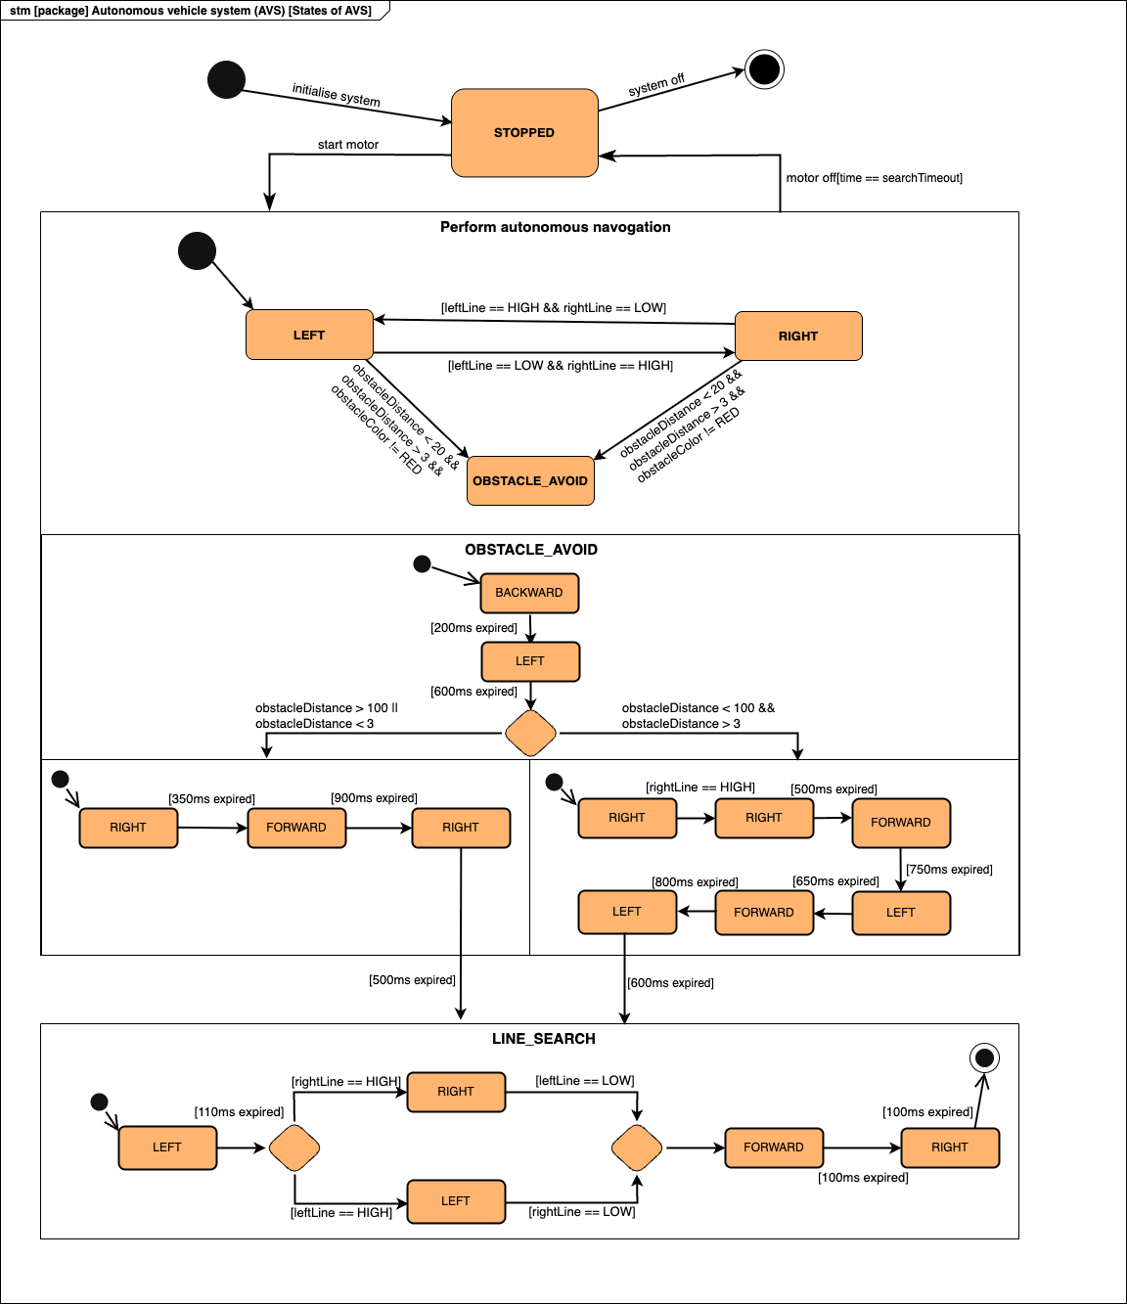
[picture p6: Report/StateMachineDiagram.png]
    
    \caption{State Machine diagram}
    \label{fig:state machine-diagram}
\end{figure}

\clearpage
\begin{figure}[H]
    \centering
    \begin{adjustbox}{max width=\textwidth, max height=0.9\textheight}
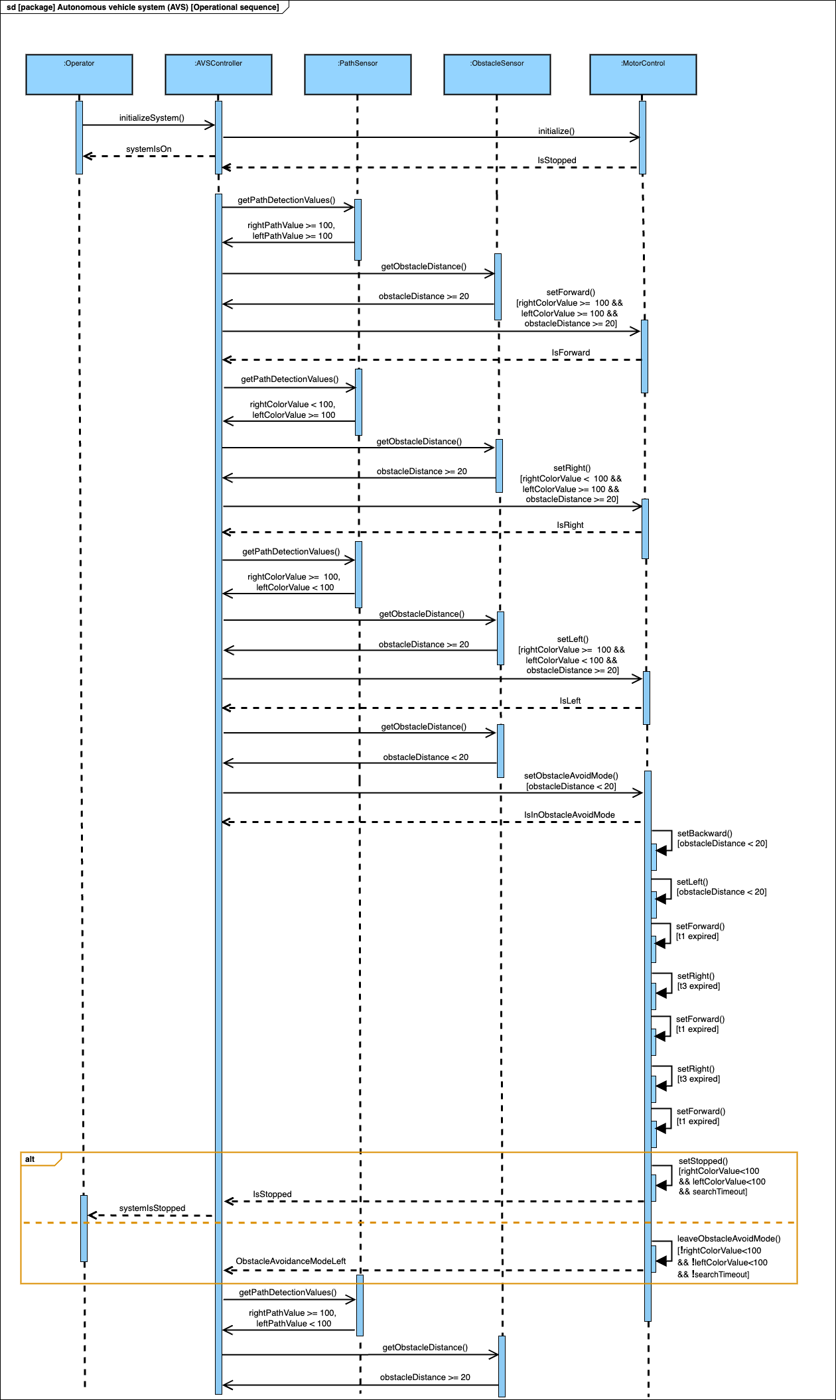
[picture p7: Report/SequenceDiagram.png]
        
    \end{adjustbox}
    \caption{Sequence diagram}
    \label{fig:seq}
\end{figure}

\clearpage
\begin{figure}[ht]
    \centering
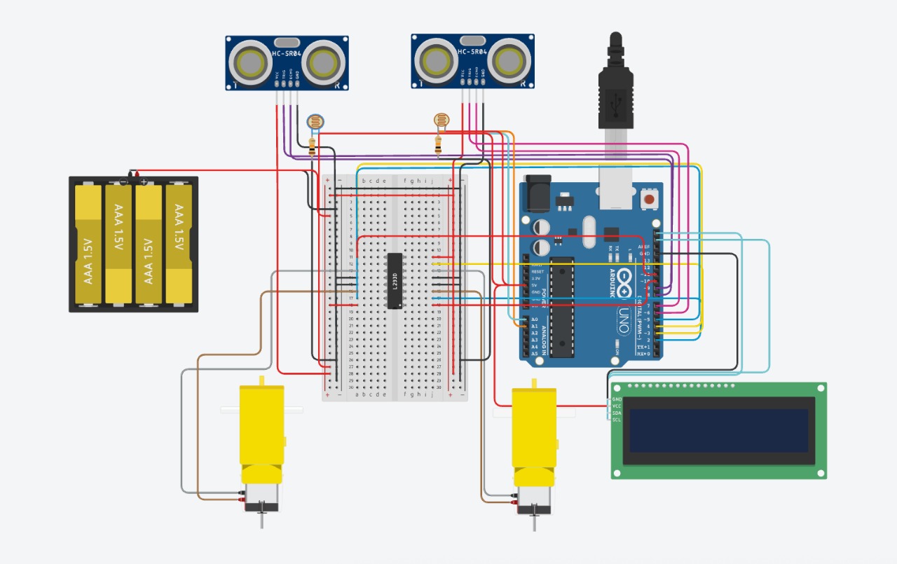
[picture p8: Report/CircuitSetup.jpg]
    
    \caption{Tinker Cad Simulation showing a complete circuit layout}
    \label{fig:CircuitSetup}
\end{figure}

    \begin{figure}[H]
    \centering
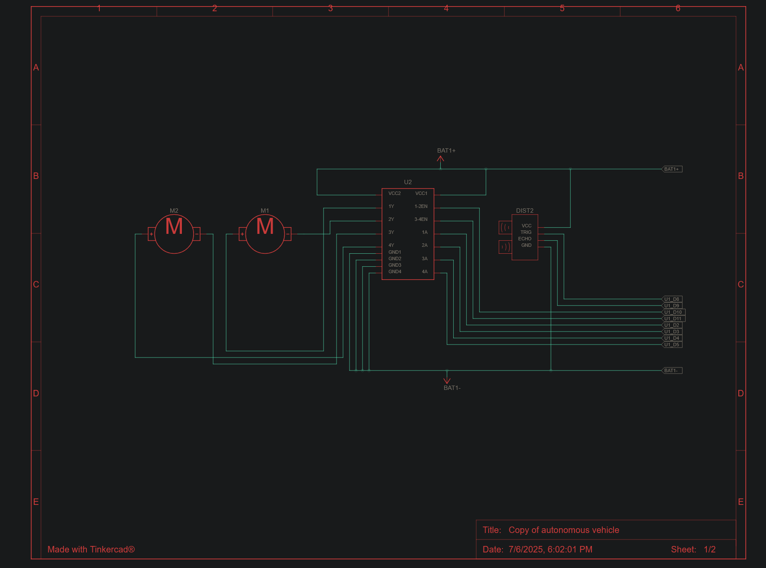
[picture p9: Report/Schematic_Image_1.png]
    
    \caption{Schematic for motor driver connection along with arduino, motors, ultrasonic sensors}
    \label{fig:Schematic}
\end{figure}

\clearpage

\begin{table}[H]
\centering
\caption{Robot State Behavior Summary}
\label{tab:behavior}
\begin{tabular}{|l|l|l|l|}
\hline
\textbf{State} & \textbf{Trigger Condition} & \textbf{Primary Action} & \textbf{Exit Condition} \\ \hline
\texttt{LEFT} & Left sensor on line & \texttt{turnLeft()} & Right sensor on line \\ \hline
\texttt{RIGHT} & Right sensor on line & \texttt{turnRight()} & Left sensor on line \\ \hline
\texttt{OBSTACLE\_AVOID} & \begin{tabular}[c]{@{}l@{}}Object in 3–20 cm\\ and not red\end{tabular} & \begin{tabular}[c]{@{}l@{}}Multi-step\\ bypass sequence\end{tabular} & Maneuver completion \\ \hline
\texttt{LINE\_SEARCH} & Both sensors off line & \begin{tabular}[c]{@{}l@{}}Scan left and right\\ for the line\end{tabular} & \begin{tabular}[c]{@{}l@{}}Line reacquired or\\ timeout expires\end{tabular} \\ \hline
\end{tabular}
\end{table}

\begin{table}[H]
\centering
\begin{adjustbox}{width=0.7\textwidth}
\begin{tabular}{|l|l|}
\hline
\textbf{Electronic Components} & \textbf{Description} \\ 
\hline
Ultrasonic Sensor (HC-SR04) & Used for detecting obstacle distance \\ 
\hline
Motor Driver (L298N) & Used for stepping down voltage and operating motors \\ 
\hline
Infrared sensors (KY-033) & Used for detecting black lines \\ 
\hline
Color sensor (TCS3200) & Used for detecting obstacle color \\ 
\hline
Arduino Uno R4  & used as the brain of the vehicle \\ 
\hline
Conrad LiPo battery 3200mah& Used to supply power to all componments \\ 
\hline
\end{tabular}
\end{adjustbox}
\caption{A quick brief info about the supplied electronic components}
\label{tab:Electronic Components}
\end{table}

    \begin{figure}[H]
    \centering
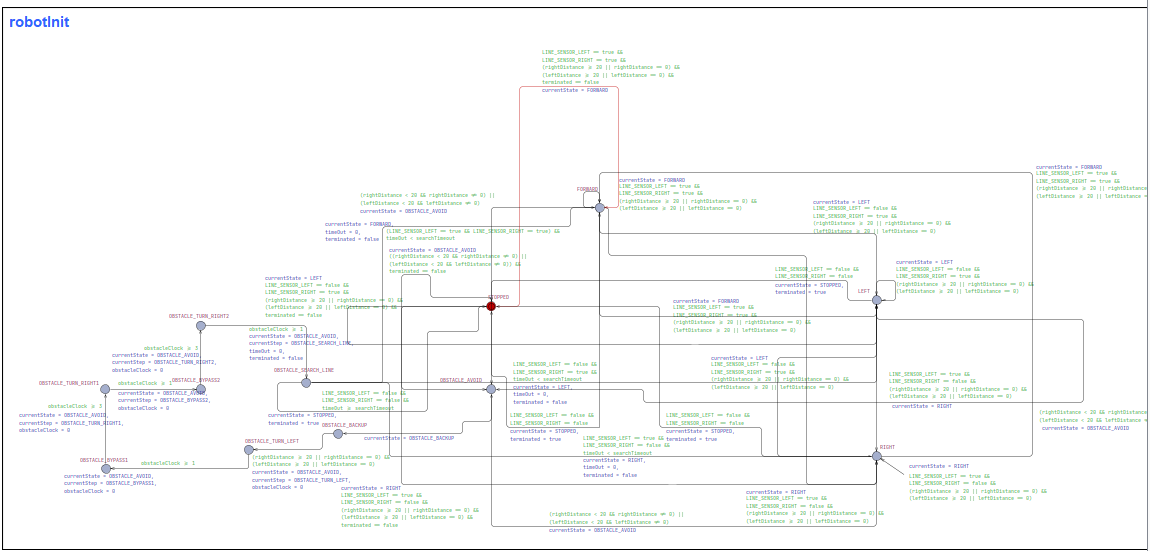
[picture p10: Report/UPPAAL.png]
    
    \caption{UPPAAL implementation for the entire system}
    \label{fig:UPPAAL}
    \textit{Note: The full code of the UPPAAL system is provided in the git repository}
\end{figure}

\end{document}

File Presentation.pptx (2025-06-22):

## Systems Engineering & Prototyping

Presented by:
Amer Mohamed Ahmed Mohamed Ali
Badhan Sadim Rahman
Shushkova Daria
Sysoev Andrey

1

## Objective & Hardware Components

- Objective:

To build an autonomous vehicle that:
- Follows a line (path)
- Detects and avoid obstacles in its path

- IR Sensors
- Ultrasonic Sensors
- DC Motors
- Arduino
- Battery
- Motor Driver

- Components:

## Motivation

1. Solving Real-World Problems
- Simulating autonomous behaviours like line following and obstacle avoidance.
2. Interdisciplinary Learning
- Engineering Design: Prototyping and system modelling
- Software: Control logic and algorithm development
- Hardware: Sensor integration and circuit implementation
- Systems Engineering: System design (SysML diagrams), requirements, testing
3. Engineering Creativity
- Handling vehicle behaviour under hardware constraints: speed control, sensor calibration, manoeuvring.

## Challenges & Solutions

## Initially designed State Machine

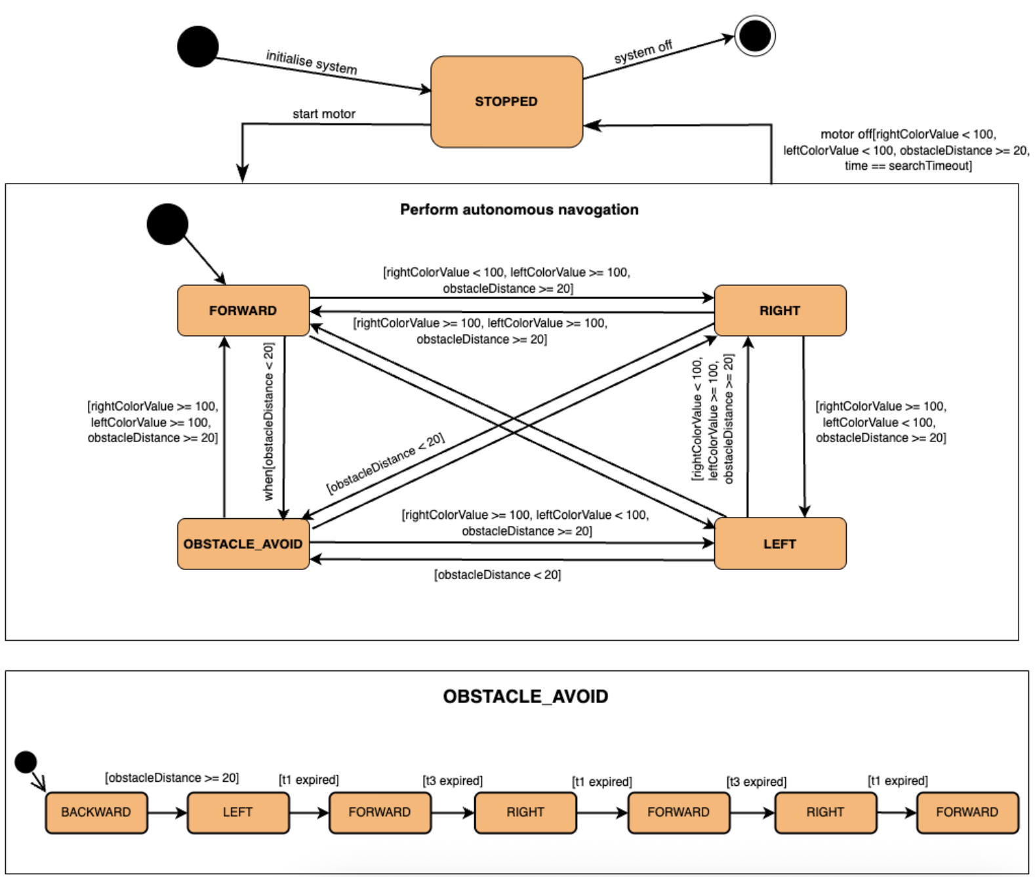
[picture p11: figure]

## Initially designed State Machine

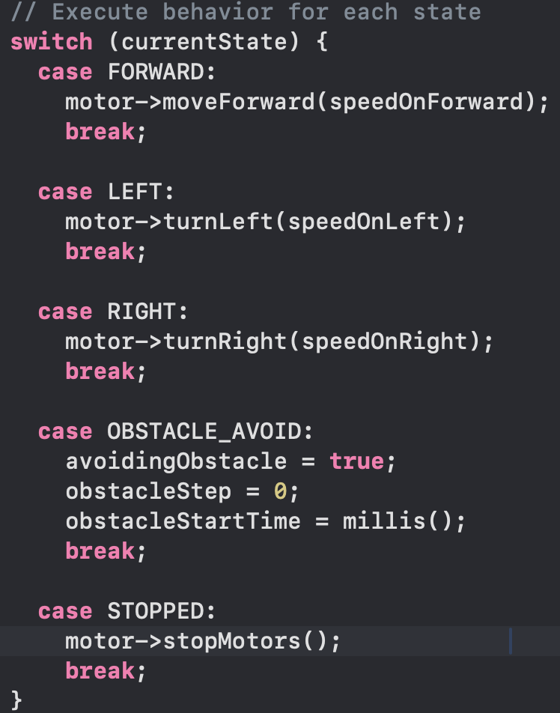
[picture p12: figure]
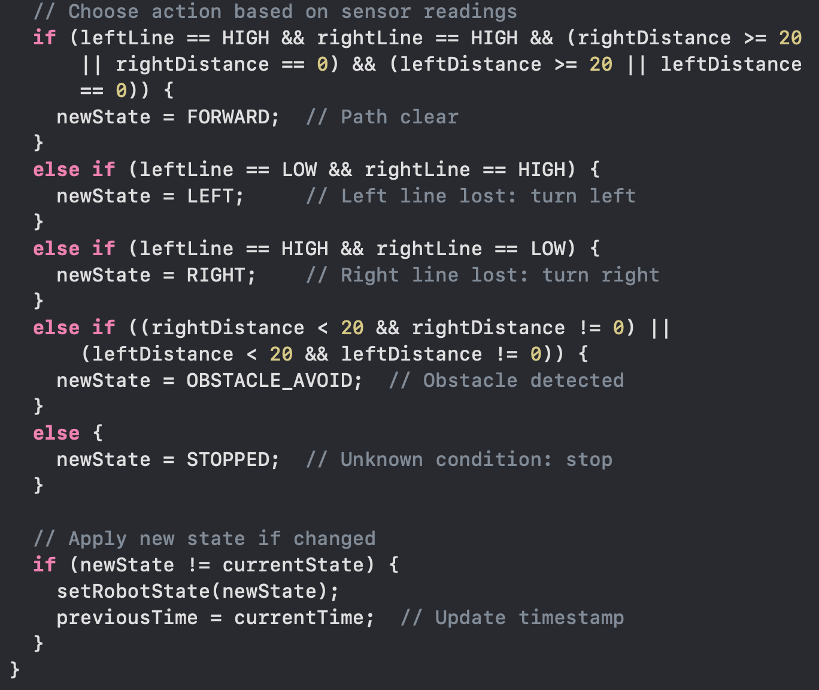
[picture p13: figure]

## Initially designed State Machine

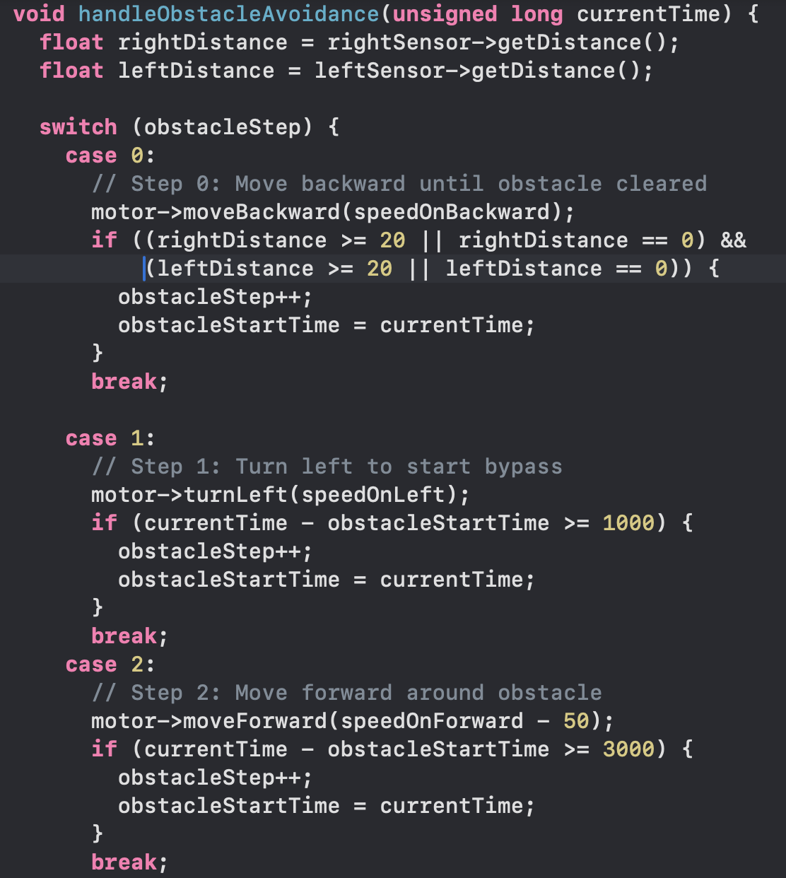
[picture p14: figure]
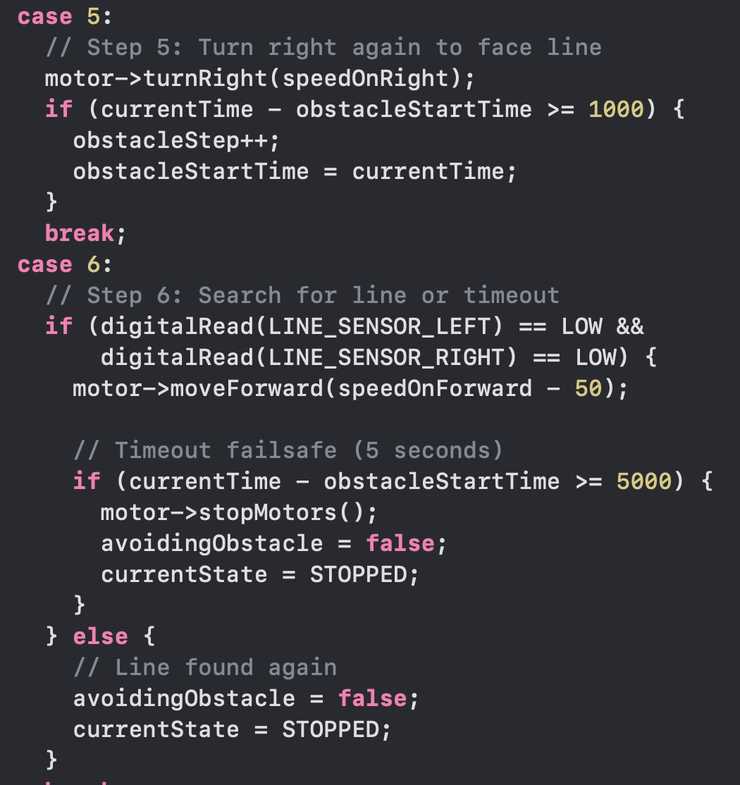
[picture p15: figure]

## Updated State Machine


## Updated State Machine

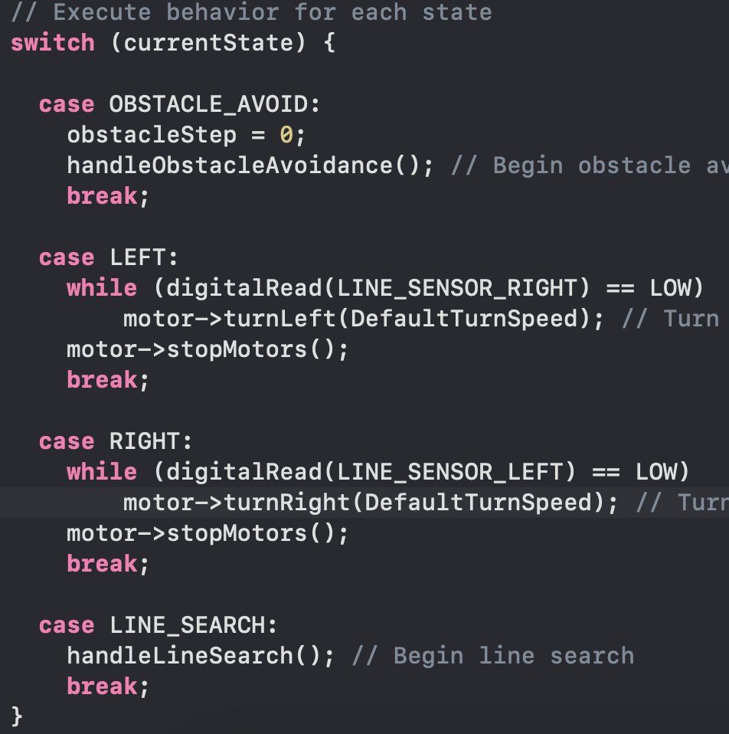
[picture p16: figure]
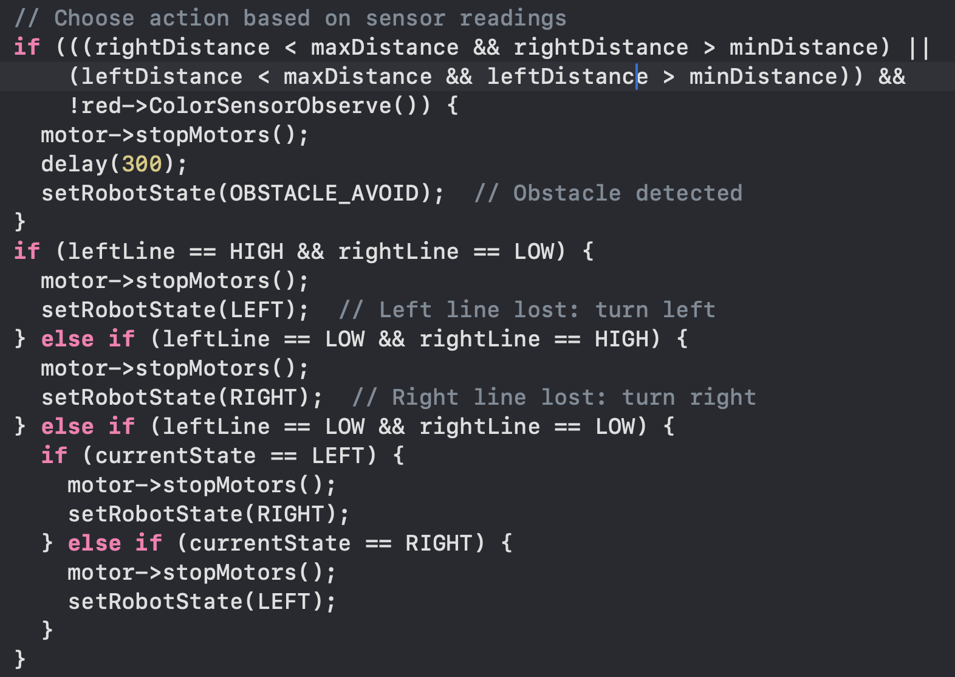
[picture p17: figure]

## Updated State Machine

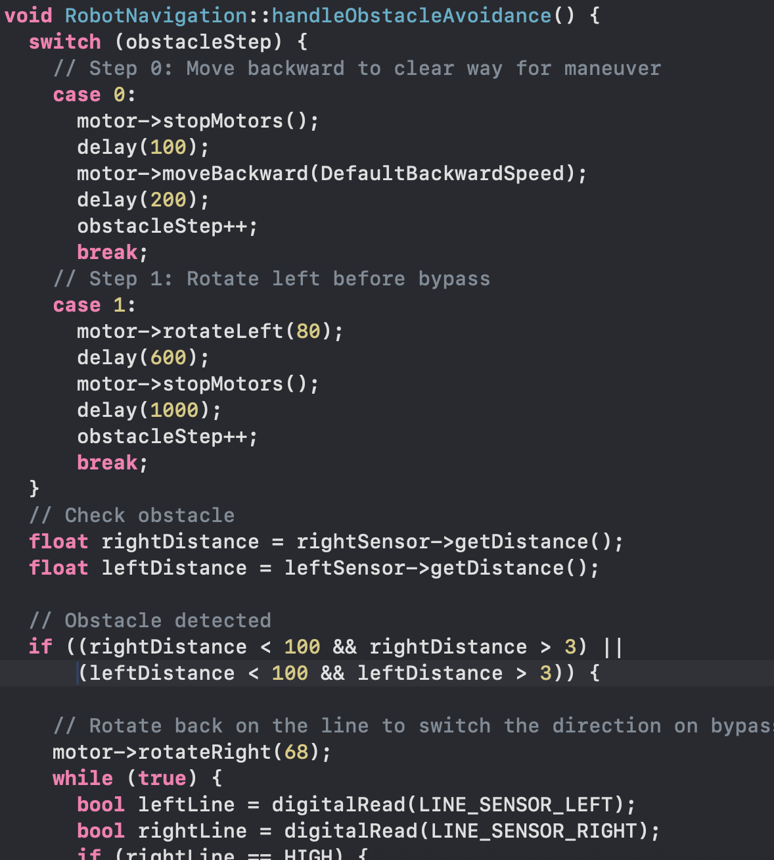
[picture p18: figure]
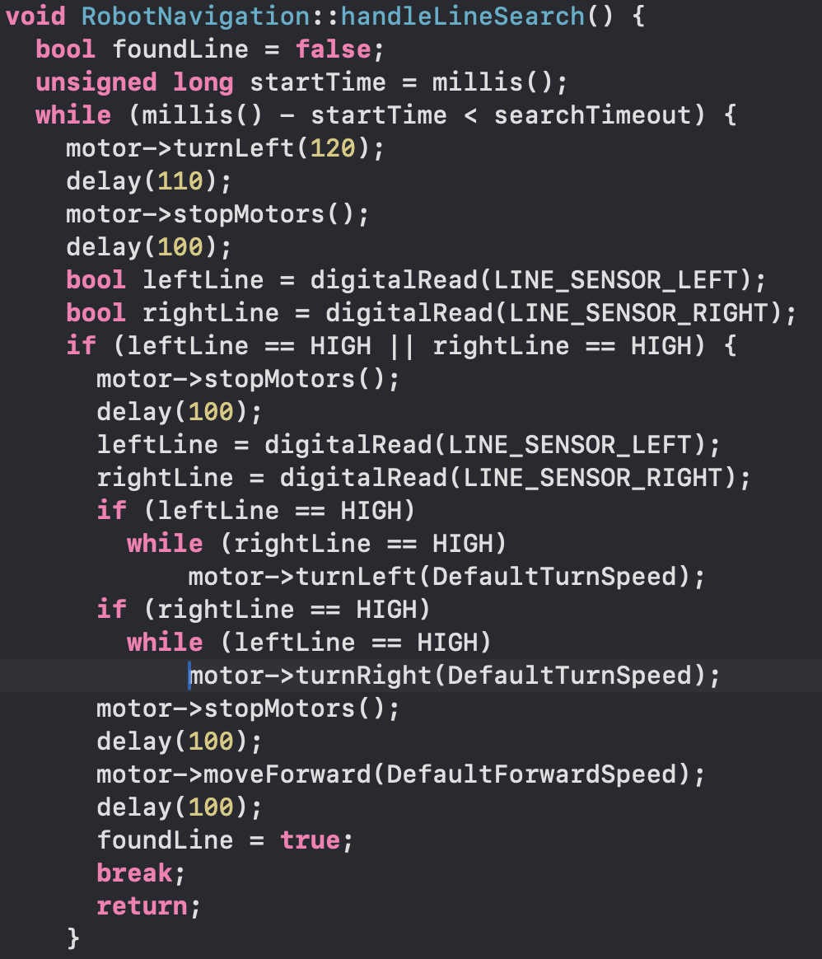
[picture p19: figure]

## Mechanical Fit

The Challenge:
- Initial 3D-printed parts were designed to precise dimensions and were designed quite thin to meet time constraint for printing.
- After printing testing these parts on the actual chassis, they did not fit well due to real-world imperfections and the 3D printer errors.

## Mechanical Fit

The Solution:
- Redesigned the parts to be thicker, less rigid, and more adaptable.
- Included some tolerances in the designed parts to compensate errors resulted from printing
- Added slots to the IR sensor mounts to enable easy location tuning without constraints.

## Wiring Management

The Challenge:
- The initial wiring was disorganized, with excessively long cables.
- This created a "messy" look and posed a functional risk, as wires could snag on moving parts or the environment, interrupting the vehicle's movement.

## Wiring Management

The Solution:
- Implemented a wire management strategy using wire clips and duct tape for a secure and neat fit
- This kept the wiring contained, orderly, and clear of any moving components.

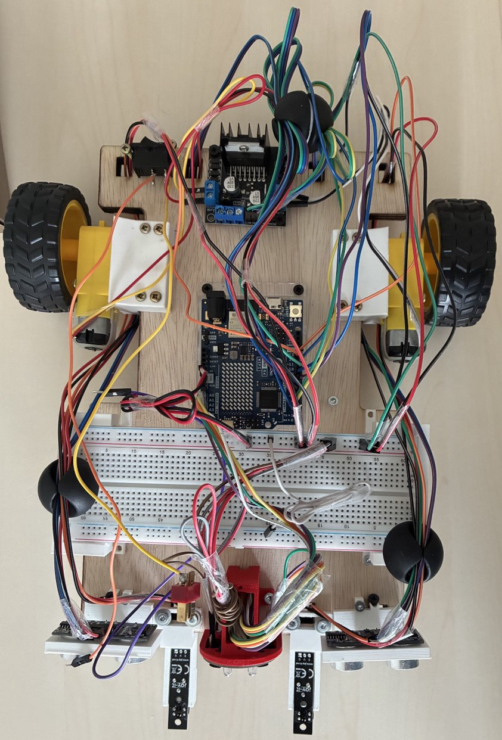
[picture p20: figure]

## Weight Distribution

The Challenge:
- In the initial design, the battery was placed at the front of the vehicle horizontally for easy access.
- During testing, this caused a critical imbalance, preventing the wheels from gaining proper traction. Thus, The vehicle struggled to move correctly.

## Weight Distribution

The Solution:
- Instead of a redesign, we added heavy bolts to the rear of the chassis to act as counterweights.
- This shifted the centre of gravity to the back, allowing the wheels to function properly.

## IR Sensors Configuration

The Challenge:
- The physical distance between our two IR sensors was much wider than the actual black line used on the track.
- Code expected a LOW signal to indicate "line detected”. It caused incorrect logic and movement.

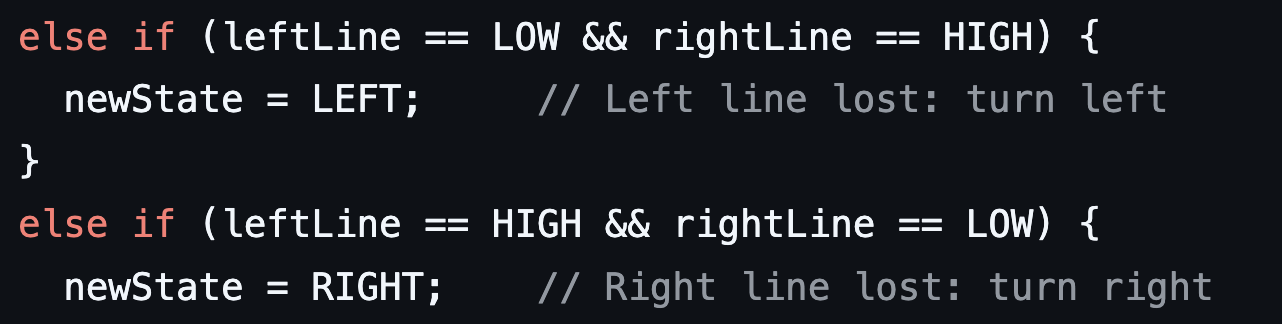
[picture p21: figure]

## IR Sensors Configuration

The Solution:
- Adjusted the Code, inverting the line detection to HIGH instead of LOW
- Adjusted the sensor spacing to be reasonable relative to the line thickness

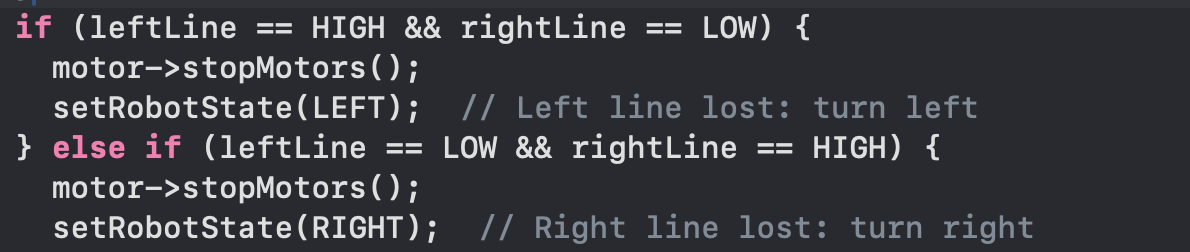
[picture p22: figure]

## Ultrasonic Configuration

The Challenge :
- The ultrasonic sensor was initially configured to detect only maximum distance (e.g.< 20 cm), without initialization of min range.

## Ultrasonic Configuration

The Solution:
- Implemented echo validation to ensure ping response falls within a practical range between minimum and maximum distance (e.g. 3 cm and 20 cm).

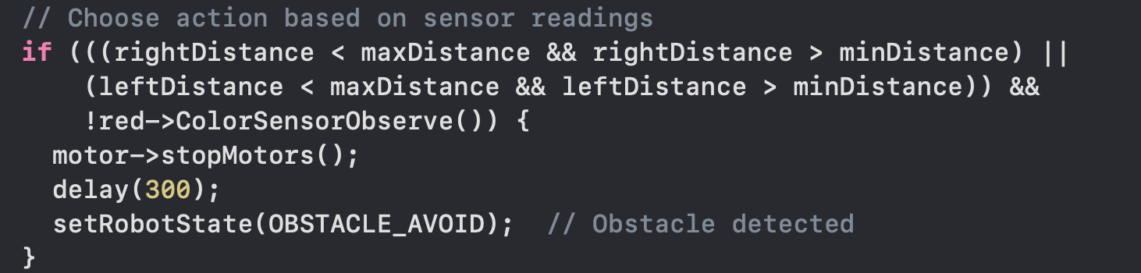
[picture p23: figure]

## Conclusion & Key Learnings

- Design for Imperfection: Real-world hardware requires more tolerance and adjustability than CAD models suggest.
- Adaptability is Key: Being able to solve problems with code (like the sensor logic) can be faster and more efficient than making physical changes.
- Iterative Testing is Crucial: The most effective solutions were found through constant testing, observation, and incremental adjustments to both hardware and software.

## Q&A

- Thank you!
- We’re happy to answer your questions.

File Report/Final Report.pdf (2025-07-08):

# Design and Implementation of a Line Following and Obstacle Avoidance Robot

Mohamed Amer∗

, Daria Shushkova∗

,Andrey Sysoev∗

, Sadim Rahman∗
∗Systems Engineering and Prototyping, BSc Electronic Engineering Hochschule Hamm-Lippstadt, Lippstadt, Germany {mohamed-ahmed-mohamed-ali.amer, daria.shushkova, andrey.sysoev, sadim-rahman.badhan}@stud.hshl.de
I. INTRODUCTION
This project focuses on the development of a simple mobile robot that can autonomously follow a black line on a white surface and avoid obstacles placed in its path. The robot uses infrared sensors to detect the line and an ultrasonic sensor to detect nearby objects. An Arduino microcontroller is used to process sensor inputs and control motors accordingly.

II. SYSTEM DESIGN AND ENGINEERING
The robot design was developed based on tasks and milestones defined at the beginning of the project. These included line following, obstacle detection and avoidance, and integration of all components into a working prototype. It uses two infrared (IR) sensors to detect the black line and an ultrasonic sensor to measure the distance from obstacles. These sensors send signals to an Arduino Uno, that acts as the main controller.
The Arduino processes data and decides how the system should respond: either adjusting its path to stay on the line or stopping and maneuvering around an obstacle. Movement is handled by two DC motors controlled through an L298N motor driver.
Power is provided by a 9V battery pack, with regulation to supply the required voltages for the microcontroller and sensors. A simplified block diagram of the system is shown in Fig. 2
The vision of a system started with creating SysML diagrams to preserve and structure our project. It has the four Pillars of SysML:
- Requirements modeling (e.g., requirement diagram)
- Parametric modeling
- Structural modeling (e.g., Block Definition diagrams (BDD), Internal Block diagrams (IBD))
- Behavioral modeling (e.g., Use Case diagrams, Activity Diagrams, Sequence Diagrams, State Machine Diagrams)
1) Requirement Diagram
It contains both functional and nonfunctional requirements of the autonomous vehicle system. These include navigation, obstacle handling, speed optimization, and route management, with their derived requirements and hardware components.
See Fig 3 the Requirement diagram.
2) Parametric Diagram
The Parametric Diagram define parametric relationships between properties of blocks. This section uses parametric diagrams to represent mathematical and physical constraints of system behavior. See Fig 4 the Parametric diagram.
3) Block Definition Diagram
The Block Definition Diagram (BDD) provides a structural decomposition of the Autonomous Vehicle System. It represents the main logical blocks and how they are hierarchically related through composition relationships.

The system is broken down into three primary subsystems:
- Chassis: Includes physical mounting blocks such as the battery and breadboard holder, IR sensor holder, motor holder, and ultrasonic sensor holder.
- Controllers: Main controller (Arduino) and the motor controller block responsible for driving the actuators.
- Components: Wheels and motors, which are part of the physical actuation system.
See Fig 5 the Block Definition diagram .
4) Use Case Diagram
Use case diagram models the interactions between User (the operator) and system functionalities. The diagram focuses on a ”happy path” — Drive Autonomously, which includes supporting behaviors like:
- Adjust Speed
- Avoid Obstacle
- Follow Path

Extra behaviors such as Drive in Oval and Drive in Figure Eight are modeled as extensions of the routing logic.
See Fig 6 the Use Case diagram.
5) State Machine Diagram
The system begins in the ”stopped” state. Upon initialization,it switches to the ”perform autonomous navigation” state, where it drives left or right based on the input of the line-following sensor. If obstacle has been detected, system transitions to the ”obstacle avoid” state.

In ”obstacle avoid”, the vehicle maneuvers around the obstacle:
- it goes ”backward” until save distance to do a maneuver
- chooses path depending if where are walls on the ”left” or ”right”
- does ”line search” to find the path after obstacle avoidance have been completed
See Fig 7 the State Machine diagram.
6) Sequence Diagram
The Sequence Diagram shows the interaction between the Operator, AVS Controller, sensors, and motor control during autonomous navigation. The controller continuously uses path and obstacle data to send com-
mands to motors: setForward(), setLeft(), or setRight().
If an obstacle is detected, the system enters Obstacle Avoid Mode, executing timed motor actions. An alt block handles conditional stopping or recovery based on search timeout and sensor feedback.
See Fig 8 the Sequence diagram.

III. PROTOTYPING AND DESIGN

Our team was supplied with several Electronic components and a pre-designed chassis for development of the line follower vehicle. Our team was tasked to design a suitable mechanical design that would perform well in practice while utilizing all of the functionalities requested. A iterative design methodology was used to reach the final design made.

A. Electronic Components

As shown in Table IV a brief about the electronic components supplied and their purpose is mentioned. Key components that needed much attention were the infrared sensor, the battery and the motor driver. The Infrared sensor was a digital active high sensor.Thus, it was needed to be calibrated on the line we are following. Furthermore, dealing with the battery and the motor driver supplied, it was critical to ensure that voltages coming out of the motor driver voltage regulator are 5 volts. otherwise, this will expose the components to permanent damage. For safety purposes and avoiding any damaging to the components, we simulated the entire circuit in TinkerCad [2].

B. Virtual and Physical Prototypes

All of the prototyping design iterations were simulated in Solid works software. Our goal was to design as few parts as we can to avoid the given printing time limit. It was agreed on at the end to use the following parts followed by their main objective:
- 2x Motor mounts: The motor mounts were used to mount the motors in a rigid way so it can support the entire weight of the vehicle.
- 2x IR sensor mounts: The main objective is to keep the IR sensors too close to the ground to avoid lighting noise from the surrounding environment
- 2x Ultrasonic mounts: Really lightweight components just to fix the ultrasonic without causing a high penality in printing time
- battery and breadboard mount: It function is to be multifunctional part holding the breadboard on its upper side and securing the battery underneath it
Our first print trial was not so successful at the beginning due to unaccounted error in our design. Then the parts were modified to have some fit tolerance to account for the error resulting from the 3D printer. Moreover on design iterations, we included slots instead of holes for the IR sensors so their position can be easily modified if needed. A visualization of the final prototype reached is shown in Figure 1.

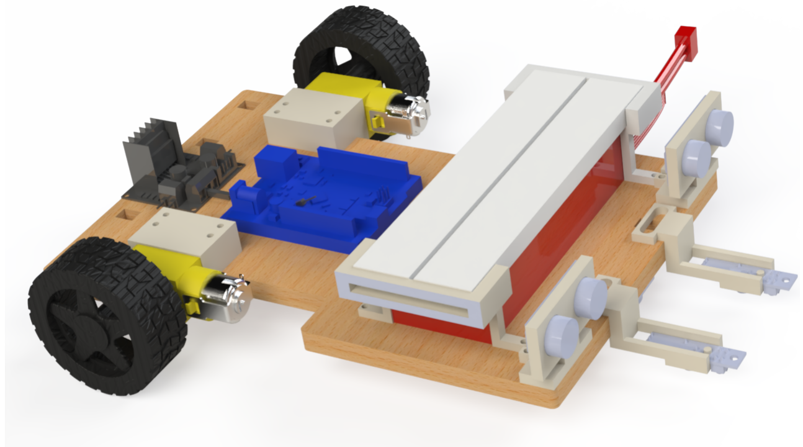
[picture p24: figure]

Fig. 1. Block diagram of the line following and obstacle avoidance robot.

C. Hardware Assembly
All components were mounted on a chassis and connected as per the schematic. For assembly, all of the parts were mounted using spax screws in 3 different lengths : 10mm, 16mm, 20mm with all of them being M3 diameter. Some holes in the wooden chassis were done using a drill. All of the components were mounted without any adhesive materials. In our assembly, it was made sure that all components were firmly secured in position.

IV. CIRCUIT DESIGN
The autonomous vehicle circuit integrates multiple sensor and actuator subsystems using an Arduino Uno as the main controller. The complete circuit layout simulation in tinkercad is shown in Fig. 9.
The wiring was designed to fulfill three key goals: modularity, robustness, and safe power distribution. Each subsystem was treated as an independent module, allowing for easier debugging and incremental development.
A. Sensor Integration
- Infrared Line Sensors (2x) are connected to digital input pins D12 and D13. These sensors detect the black line against the white surface, and their values are read in real-time to determine the robot’s lateral alignment.
- Ultrasonic Sensors (2x) are mounted on the front-left and front-right sides. Their trigger and echo pins are connected to D6/D7 (right) and D8/D9 (left). These provide real-time distance feedback to avoid collisions.
- Color Sensor (1x) is connected to analog pins A0 to A4. It adds redundancy to object classification, allowing the robot to treat red-colored obstacles differently (e.g., push or bypass).
B. Actuator Wiring

The circuit schematic of the Motor Driver along with the motors and ultrasonic sensors is shown in 10.

- Motor Driver (L298N) is used to control two DC motors. It is connected to:
– PWM pins D10 and D11 for speed control
– Direction control pins D2–D5
The motors are powered directly from the 12V battery pack via the motor driver’s onboard regulator.
C. Power Management
- A 12V DC battery pack supplies power to both motors and the Arduino.
- A voltage regulator onboard the L298N downscales the 12V to 5V for the Arduino and sensors, avoiding voltage spikes and protecting delicate components.
- Decoupling capacitors are placed across power lines to minimize electrical noise and ensure stable analog sensor readings.
D. Pin Mapping Overview

The Table I shows the pins that were used in details.

TABLE I
KEY PIN ASSIGNMENTS
Component | Pin(s)
IR Sensor (Left) | D13
IR Sensor (Right) | D12
Ultrasonic Sensor (Left) | D8 (Trig), D9 (Echo)
Ultrasonic Sensor (Right) | D6 (Trig), D7 (Echo)
Left Motor | D2 (F), D3 (B), D10 (PWM)
Right Motor | D4 (F), D5 (B), D11 (PWM)
Color Sensor | A0–A4
E. Schematic Analysis

The circuit was simulated and verified using Tinkercad and real-world breadboard prototyping. Care was taken to route ground lines properly, avoid floating inputs, and apply pulldown resistors where needed.
The design emphasizes modularity, with all sensors and motors detachable via male/female header connectors for ease of maintenance and reassembly.
V. SOFTWARE IMPLEMENTATION
A. Initialization of Sensors and Actuators

### 1. Sensors Initialization:

a) Ultrasonic Sensors (Left/Right) — Pins for the ultrasonic sensors are defined in the file ’UltrasonicSensor.h’. They are set up and initialized in the ’UltrasonicSensor.cpp’ and ’main.cpp’ files. Relevant snippets are shown below:

// Ultrasonic sensor pin definitions
#define LEFT_TRIG_PIN 8

#define LEFT_ECHO_PIN 9

#define RIGHT_TRIG_PIN 6

#define RIGHT_ECHO_PIN 7

Listing 1. Pin definitions in UltrasonicSensor.h

// Set trigger as output and echo as input void UltrasonicSensor::begin() { pinMode(trigPin, OUTPUT);
pinMode(echoPin, INPUT);
}

Listing 2. Pin setup in UltrasonicSensor.cpp

// Create hardware instances
UltrasonicSensor rightUltrasonic( RIGHT_TRIG_PIN,
RIGHT_ECHO_PIN);
UltrasonicSensor leftUltrasonic( LEFT_TRIG_PIN,
LEFT_ECHO_PIN);
RobotNavigation robotNav(
&rightUltrasonic,
&leftUltrasonic,
&motor);

// Initialize ultrasonic sensors void setup() {
rightUltrasonic.begin();
leftUltrasonic.begin();
}

Listing 3. Sensor initialization in main.cpp

b) IR Sensors (Left/Right) — Pins for the IR sensors are defined in ’RobotNavigation.h’ and initialized in ’Robot-Navigation.cpp’ and in ’main.cpp’. Relevant snippets are shown below:

// Line sensor digital pins
#define LINE_SENSOR_LEFT 13

#define LINE_SENSOR_RIGHT 12

Listing 4. IR sensor pin definitions in RobotNavigation.h

void RobotNavigation::begin() { pinMode(LINE_SENSOR_LEFT, INPUT); pinMode(LINE_SENSOR_RIGHT, INPUT);
}

Listing 5. IR sensor pin initialization in RobotNavigation.cpp

void setup() {
// Start navigation system

robotNav.begin();
}

Listing 6. IR sensor pin initialization in main.cpp

c) Color Sensor — Pins for the color sensor are defined in ’ColorSensor.h’ and initialized in ’ColorSensor.cpp’. Relevant snippets are shown below:

// Pin definitions
#define COLOR_SENSOR_OUTPUT_FREQUENCY_INPUT_S0 ,→ A0

#define COLOR_SENSOR_OUTPUT_FREQUENCY_INPUT_S1 ,→ A1

#define COLOR_SENSOR_PHOTODIODE_INPUT_S2 A2 #define COLOR_SENSOR_PHOTODIODE_INPUT_S3 A3 #define COLOR_SENSOR_OUTPUT_PIN A4

Listing 7. Color sensor pin definitions in ColorSensor.h

void ColorSensor::ColorSensorInit() { pinMode(
COLOR_SENSOR_OUTPUT_FREQUENCY_INPUT_S0, OUTPUT);
pinMode(
COLOR_SENSOR_OUTPUT_FREQUENCY_INPUT_S1, OUTPUT);
pinMode(
COLOR_SENSOR_PHOTODIODE_INPUT_S2, OUTPUT);
pinMode(
COLOR_SENSOR_PHOTODIODE_INPUT_S3, OUTPUT);
pinMode(
COLOR_SENSOR_OUTPUT_PIN,
INPUT);

digitalWrite(
COLOR_SENSOR_OUTPUT_FREQUENCY_INPUT_S0, HIGH); // Full scale
digitalWrite(
COLOR_SENSOR_OUTPUT_FREQUENCY_INPUT_S1, LOW); // Frequency scaling = 20%
}

Listing 8. Color sensor pin initialization in ColorSensor.cpp

### 2. Actuators (Motors) Initialization: Motor Control Pins

are defined in the file ’MotorControl.h’. Their setup and initialization are made in the ’main.cpp’ file. Relevant snippets are shown below:

// Motor control pin definitions
#define LEFT_MOTOR_SPEED_PIN 10 #define RIGHT_MOTOR_SPEED_PIN 11 #define LEFT_MOTOR_FORWARD_PIN 2 #define LEFT_MOTOR_BACKWARD_PIN 3 #define RIGHT_MOTOR_FORWARD_PIN 4 #define RIGHT_MOTOR_BACKWARD_PIN 5

Listing 9. Pin definitions in MotorControl.h

// Create hardware instances MotorControl motor;

RobotNavigation robotNav(
&rightUltrasonic,
&leftUltrasonic,
&motor
);
// Arduino initialization

void setup() {
// Setup motor pins as outputs pinMode(LEFT_MOTOR_SPEED_PIN, OUTPUT); pinMode(RIGHT_MOTOR_SPEED_PIN, OUTPUT); pinMode(LEFT_MOTOR_FORWARD_PIN, OUTPUT); pinMode(LEFT_MOTOR_BACKWARD_PIN, OUTPUT); pinMode(RIGHT_MOTOR_FORWARD_PIN, OUTPUT); pinMode(RIGHT_MOTOR_BACKWARD_PIN, OUTPUT); ...
}

Listing 10. Pins initialization in main.cpp

Key Initialization Features:
1) Pin Abstraction
- Hardware pins are abstracted via #define macros.
- Logical separation of sensor and actuator types.
2) Modular Initialization
- Each sensor type has its own initialization routine.
- Motor control setup is centralized in main.cpp.
3) Hardware–Software Mapping
- On Fig. 2, the block diagram shows how each hardware component is mapped to specific software-controlled pins in the Arduino controller.
This summary ensures the reader understands the overarching design—pin abstraction, modular setup, mapping, and your carefully ordered startup sequence—before diving into higher-level behavior logic.
B. Movement Control Algorithms

### 1. Core Movement Methods:

a) Forward and Backward Motion - The robot’s linear motion is achieved through symmetric control of both motors using Pulse Width Modulation (PWM) for speed regulation. The direction of rotation is set by toggling the appropriate H-bridge control pins. The methods of the MotorControl class in ’MotorControl.cpp’ show the implementation of forward and reverse movement:

// Move robot straight forward at given speed void MotorControl::moveForward(int speed) { analogWrite(LEFT_MOTOR_SPEED_PIN, speed); analogWrite(RIGHT_MOTOR_SPEED_PIN, speed); digitalWrite(LEFT_MOTOR_FORWARD_PIN, LOW); digitalWrite(LEFT_MOTOR_BACKWARD_PIN, HIGH); digitalWrite(RIGHT_MOTOR_FORWARD_PIN, LOW); digitalWrite(RIGHT_MOTOR_BACKWARD_PIN, HIGH); }

// Move robot straight backward at given speed void MotorControl::moveBackward(int speed) { analogWrite(LEFT_MOTOR_SPEED_PIN, speed); analogWrite(RIGHT_MOTOR_SPEED_PIN, speed); digitalWrite(LEFT_MOTOR_FORWARD_PIN, HIGH); digitalWrite(LEFT_MOTOR_BACKWARD_PIN, LOW); digitalWrite(RIGHT_MOTOR_FORWARD_PIN, HIGH); digitalWrite(RIGHT_MOTOR_BACKWARD_PIN, LOW); }

Listing 11. Forward and backward movement functions

Key Algorithm:
- PWM | signals | regulate | motor | speed | via
analogWrite().

- H-bridge circuits manage direction through digital pins.
- Equal PWM ensures coordinated, straight-line movement.
b) Pivotal Turning - For medium-radius turns, one motor is activated while the other is disabled, allowing the robot to pivot around the unpowered wheel. The turnLeft() and turnRight() methods implement this by powering one motor while setting both control pins for the other motor to LOW, causing it to freewheel or coast. This creates a smoother turn compared to a point rotation.

// Turn robot to the left
void MotorControl::turnLeft(int speed) { analogWrite(LEFT_MOTOR_SPEED_PIN, speed); digitalWrite(LEFT_MOTOR_FORWARD_PIN, LOW); digitalWrite(LEFT_MOTOR_BACKWARD_PIN, HIGH); digitalWrite(RIGHT_MOTOR_FORWARD_PIN, LOW); digitalWrite(RIGHT_MOTOR_BACKWARD_PIN, LOW); }

// Turn robot to the right
void MotorControl::turnRight(int speed) { analogWrite(RIGHT_MOTOR_SPEED_PIN, speed); digitalWrite(LEFT_MOTOR_FORWARD_PIN, LOW); digitalWrite(LEFT_MOTOR_BACKWARD_PIN, LOW); digitalWrite(RIGHT_MOTOR_FORWARD_PIN, LOW); digitalWrite(RIGHT_MOTOR_BACKWARD_PIN, HIGH); }

Listing 12. Single-wheel pivot turn functions

Key Algorithm:
- Only one motor is actively powered for the turn.
- The other motor is disabled and its wheel is allowed to coast, serving as the pivot point.
- The turning radius is determined by the robot’s geometry and the speed of the powered wheel.
c) In-Place Rotation - In-place rotation is accomplished by driving both motors in opposite directions at equal speed. This results in a zero turning radius, allowing the robot to pivot around its center. The technique is useful in constrained environments or for rapid heading adjustments.

// Rotate robot to the right
void MotorControl::rotateRight(int speed) { analogWrite(RIGHT_MOTOR_SPEED_PIN, speed); analogWrite(LEFT_MOTOR_SPEED_PIN, speed); digitalWrite(LEFT_MOTOR_FORWARD_PIN, HIGH); digitalWrite(LEFT_MOTOR_BACKWARD_PIN, LOW); digitalWrite(RIGHT_MOTOR_FORWARD_PIN, LOW); digitalWrite(RIGHT_MOTOR_BACKWARD_PIN, HIGH); }

// Rotate robot to the left
void MotorControl::rotateLeft(int speed) { analogWrite(RIGHT_MOTOR_SPEED_PIN, speed); analogWrite(LEFT_MOTOR_SPEED_PIN, speed); digitalWrite(LEFT_MOTOR_FORWARD_PIN, LOW); digitalWrite(LEFT_MOTOR_BACKWARD_PIN, HIGH); digitalWrite(RIGHT_MOTOR_FORWARD_PIN, HIGH); digitalWrite(RIGHT_MOTOR_BACKWARD_PIN, LOW); }

Listing 13. Counter-rotational in-place turning

Key Algorithm:

- Opposite motor directions produce a central rotation.
- Equal PWM ensures balanced torque and pivoting.
- Enables highly responsive directional changes.
d) Stopping Mechanism - To halt motion, both motors are actively short-braked by setting both control lines to HIGH. Simultaneously, PWM is set to its maximum to ensure full coil engagement. This braking approach ensures faster and more stable stops compared to passive coasting.

// Stop robot
void MotorControl::stopMotors() { analogWrite(LEFT_MOTOR_SPEED_PIN, 255); analogWrite(RIGHT_MOTOR_SPEED_PIN, 255); digitalWrite(LEFT_MOTOR_FORWARD_PIN, HIGH); digitalWrite(LEFT_MOTOR_BACKWARD_PIN, HIGH); digitalWrite(RIGHT_MOTOR_FORWARD_PIN, HIGH); digitalWrite(RIGHT_MOTOR_BACKWARD_PIN, HIGH); }

Listing 14. Active braking mechanism

Key Algorithm:
- Short-circuit braking is applied to both motors.
- Ensures rapid deceleration and positional stability.
- Full PWM maximizes current for immediate response.

### 2. Parameterization and Tuning: To balance power con-

sumption, control responsiveness, and maneuverability, a set of predefined constants are used for speed tuning. These constants are defined in the header file RobotNavigation.h and used throughout the motion control routines.

// Speed configurations
#define DefaultTurnSpeed 140

#define DefaultRotateSpeed 120 #define DefaultForwardSpeed 120 #define DefaultBackwardSpeed 80

Listing 15. Speed tuning parameters

Tuning Principles:
- High Turn Speed: The turning speed (140) is set higher than the forward speed to ensure rapid and responsive correction when the robot deviates from the line.
- Controlled Rotation and Forward Motion: Forward and rotation speeds (120) are balanced to provide stable movement during standard navigation and obstacle avoidance maneuvers.
- Reduced Reverse Speed: Reverse motion uses a lower PWM value (80) for increased precision and safety, particularly when backing away from an obstacle.
- PWM Range: All values are calibrated within the 0–255 PWM range to prevent motor saturation while providing adequate torque.

### 3. Real-World Execution Flow: The robot’s low-level

movement primitives are integrated with sensor feedback to execute complex, high-level behaviors. The obstacle avoidance routine is a key example, combining multiple motion types in a timed and sensor-driven sequence.

// Behavior for obstacle avoidance sequence
void RobotNavigation::handleObstacleAvoidance() { switch (obstacleStep) {

// Move backward to clear way for maneuver case 0:
motor->stopMotors();
delay(100);
motor->moveBackward(DefaultBackwardSpeed); delay(200);
obstacleStep++;
break;
// Rotate left before bypass case 1:
motor->rotateLeft(80);
delay(600);
motor->stopMotors();
delay(1000);
obstacleStep++;
break;
}

// Check obstacle on the left side
float rightDistance = rightSensor->getDistance(); float leftDistance = leftSensor->getDistance();

// Scenario 1: Obstacle detected
if ((rightDistance < 100 && rightDistance > 3) || (leftDistance < 100 && leftDistance > 3)) {

/* Rotate right to recover straight position. The while loop allows to find line back by rotating right until line is detected again */

motor->rotateRight(68);
while (true) {
bool leftLine = digitalRead(LINE_SENSOR_LEFT); bool rightLine =
,→ digitalRead(LINE_SENSOR_RIGHT);
if (rightLine == HIGH) {
motor->stopMotors();
delay(500);
break;
}
}

/* Once recovered the straight position, rotate right to bypass from the right side which is clear from obstacles */

motor->rotateRight(75);
delay(500);

/* Bypass the obstacle by executing a pre-tuned multi-step maneuver, developed through testing with the specific hardware and environment conditions */

// Scenario 2: Obstacle is not detected
} else {

// Rotate slightly right
motor->rotateRight(75);
delay(350);

/* Execute bypass with pre-tuned multi-step maneuver, developed through testing */
}

/* In the end of bypass, switch to LINE_SEARCH to reacquire the path */ currentState = LINE_SEARCH; setRobotState(LINE_SEARCH);
}

Listing 16. Excerpt from the Obstacle Avoidance Sequence

This | procedure | shows | how | low-level | primitives

(moveBackward, rotateLeft, etc.) are composed
into a stateful, adaptive sequence. By layering control logic over robust actuator routines, the system achieves both predictability and adaptability in dynamic environments.
C. Behavioral Decision Logic
The robot’s autonomy is governed by a state machine architecture implemented in the RobotNavigation class. This design ensures that the robot transitions between welldefined behaviors based on sensor inputs. The logic is visualized in the state machine diagram in Fig 7 and implemented in the methods below.

### 1. State Machine Architecture: The core of the decision-

making process is located in the updateNavigation() method in ’RobotNavigation.cpp’, which runs continuously. It performs the reading of all relevant sensors and the usage of a prioritized decision tree to select the robot’s next state.
a) Core States - The primary operational states are defined as macros in ’RobotNavigation.h’.

// Robot states
#define OBSTACLE_AVOID 0

#define LEFT 1

#define RIGHT 2

#define LINE_SEARCH 3

Listing 17. State Definitions in RobotNavigation.h

b) State Transition Logic - The state transition logic is based on a priority-based sequence implemented in the updateNavigation() method, where the obstacle avoidance is the highest priority.

void RobotNavigation::updateNavigation() {
// Read line and obstacle sensors
int leftLine = digitalRead(LINE_SENSOR_LEFT); int rightLine =
,→ digitalRead(LINE_SENSOR_RIGHT); float rightDistance =
,→ rightSensor->getDistance(); float leftDistance =
,→ leftSensor->getDistance();

// Decision Tree
// Priority 1: Obstacle detection
if (((rightDistance < maxDistance && rightDistance > minDistance) || (leftDistance < maxDistance && leftDistance > minDistance)) && !red->ColorSensorObserve()) { motor->stopMotors();
delay(300);
setRobotState(OBSTACLE_AVOID); }

// Priority 2: Line following

// Right sensor lost the line
if (leftLine == HIGH && rightLine == LOW) { motor->stopMotors();
setRobotState(LEFT); // Turn left

// Left sensor lost the line
} else if (leftLine == LOW && rightLine == ,→ HIGH) {
motor->stopMotors();
setRobotState(RIGHT); // Turn right

// Both sensors lost the line
} else if (leftLine == LOW && rightLine == ,→ LOW) {
// Invert last state
if (currentState == LEFT) { motor->stopMotors();
setRobotState(RIGHT);
} else if (currentState == RIGHT) { motor->stopMotors();
setRobotState(LEFT);
}
}
}

Listing 18. Decision Logic in RobotNavigation.cpp

An important feature of the decision logic is the integration of the color sensor. The robot should only enter the OBSTACLE_AVOID state if the detected object is NOT RED, allowing it to push red objects off the line and continue following it.

### 2. State-Specific Behaviors: Once a state is set via

setRobotState() method, a specific handler function is executed.
a) OBSTACLE AVOID State — This is a multi-step routine managed by the obstacleStep attribute of the RobotNavigate class. It does not execute in a single function call but progresses through a sequence.
- Step 0 & 1: The robot first moves backward to create space, then rotates to face a new heading.
- Conditional Bypass: After the initial turn, the robot re-checks for another obstacle on the left. If one is detected within a 3-100 cm range, a longer, more complex bypass maneuver is executed: the robot first rotates right to recover its original position using the line sensors, and then rotates right again to initiate a bypass from the opposite side, which is presumed clear. Otherwise, a shorter maneuver is performed to return to the path (see Fig. 7 and the code snippet in Listing 16)
- Exit Condition: Upon completing the bypass maneuver, the robot transitions to the LINE_SEARCH state to reacquire the line.
b) LEFT and RIGHT States — These states handle the line-following course. The robot executes a pivot turn until the opposite sensor rediscovers the line, ensuring the robot straightens out. This logic applies a zig-zag pattern, allowing the robot to follow the line even through the sharpest curves.

case LEFT:
/* Turn left until the right IR sensor detects the line */

while (digitalRead(LINE_SENSOR_RIGHT) == LOW) motor->turnLeft(DefaultTurnSpeed); motor->stopMotors();
break;

case RIGHT: // The RIGHT case is symmetric ...

Listing 19. Line Correction Logic c) LINE SEARCH State — This state is triggered after the robot completes an obstacle avoidance maneuver. The logic of this state is implemented in the handleLineSearch() method in ’RobotNavigation.cpp’. The method executes a zig-zag pattern, first turning left and then right in small increments, until one of the sensors finds the line.
- Timeout Failsafe: This search is constrained by a searchTimeout of 100,000 ms. If the line is not found within this period, the routine terminates, which corresponds to the transition to the final STOPPED state in the state diagram (see Fig. 7).
- Re-alignment: Once the line is detected, a final adjustment is made to center the robot before resuming forward motion.

void RobotNavigation::handleLineSearch() { bool foundLine = false;
unsigned long startTime = millis();
while (millis() - startTime < searchTimeout) { motor->turnLeft(120);
delay(110);
motor->stopMotors();
delay(100);

bool leftLine = digitalRead(LINE_SENSOR_LEFT); bool rightLine = digitalRead(LINE_SENSOR_RIGHT);

if (leftLine == HIGH || rightLine == HIGH) { // Realignment sequence
if (leftLine == HIGH)
while (rightLine == HIGH)
motor->turnLeft(DefaultTurnSpeed);

if (rightLine == HIGH)
while (leftLine == HIGH)
motor->turnRight(DefaultTurnSpeed);

break;
}

// Try right turn if line not found and repeat motor->turnRight(DefaultTurnSpeed); delay(100);
motor->stopMotors();
delay(100);
}

Listing 20. Excerpt from the Line Search Sequence

### 3. Behavioral Characteristics Summary: The Table III

summarizes the primary state transitions. The ”Default” behavior of moving forward is the implicit action when no other trigger condition is met.

VI. GIT USAGE AND COLLABORATION

Project development was tracked using GitHub. In Table II ,The contributions of each member is shown according to the GitHub repository commits. The table can be found in the appendix.

VII. KEY ACHIEVEMENTS

The initial state machine was simulated in UPPAAL in Figure 11 flawlessly. Moreover, our autonomous car was able to follow the line smoothly, handling sharp turn at high speeds, successfully detecting obstacles and avoiding them, all of this while keeping a good accuracy of the line tracking. Moreover, we were successful in achieving successful integration of the hardware, consistency of results across multiple tests, effective collaboration using Git for version control and systematic testing and debugging approach.

ACKNOWLEDGMENT

REFERENCES

[1] Arduino Documentation. https://www.arduino.cc/en/Guide
[2] Tinkercad Simulation. https://www.tinkercad.com
[3] Uppaal Model Checker. http://www.uppaal.org/

DECLARATION OF ORIGINALITY
We hereby declare that this report is our own work and that we have acknowledged all sources used.

APPENDIX

FIGURES AND TABLES

Team Member | Number of Commits
Mohamed Amer | 30
Daria Shushkova | 72
Andrey Sysoev | 58
Sadim Rahman | 34
Total | 194

TABLE II
GITHUB COMMITS BY TEAM MEMBERS


Fig. 2. Block diagram of the robot system architecture.


Fig. 3. Requirement diagram


Fig. 4. Parametric diagram


Fig. 5. Block Definition diagram

Fig. 6. Use Case diagram


Fig. 7. State Machine diagram


Fig. 8. Sequence diagram


Fig. 9. Tinker Cad Simulation showing a complete circuit layout

Fig. 10. Schematic for motor driver connection along with arduino, motors, ultrasonic sensors

TABLE III
ROBOT STATE BEHAVIOR SUMMARY
State | Trigger Condition | Primary Action | Exit Condition
LEFT | Left sensor on line | turnLeft() | Right sensor on line
RIGHT | Right sensor on line | turnRight() | Left sensor on line
OBSTACLE_AVOID | Object in 3–20 cm and not red | Multi-step bypass sequence | Maneuver completion
LINE_SEARCH | Both sensors off line | Scan left and right for the line | Line reacquired or timeout expires
Electronic Components | Description
Ultrasonic Sensor (HC-SR04) | Used for detecting obstacle distance
Motor Driver (L298N) | Used for stepping down voltage and operating motors
Infrared sensors (KY-033) | Used for detecting black lines
Color sensor (TCS3200) | Used for detecting obstacle color
Arduino Uno R4 | used as the brain of the vehicle
Conrad LiPo battery 3200mah | Used to supply power to all componments

TABLE IV
A QUICK BRIEF INFO ABOUT THE SUPPLIED ELECTRONIC COMPONENTS


Fig. 11. UPPAAL implementation for the entire system
Note: The full code of the UPPAAL system is provided in the git repository

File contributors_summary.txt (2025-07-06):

    
Shown below is the number of commits made per user as exported from git.
    63	Daria Shushkova <dariashushkova@Darias-MacBook-Pro.local>
    58	andrey-sysoev <andrey.sysoev@stud.hshl.de>
    30	Amer195 <163016879+Amer195@users.noreply.github.com>
    27	SamRB-dev <sadimrahmanbadhon@gmail.com>
     9	DariaShushkova <daria.shushkova@stud.hshl.de>
     7	Sadim Rahman Badhan <70096616+SamRB-dev@users.noreply.github.com>

After merging the duplicate accounts
    72	Daria Shushkova <dariashushkova@Darias-MacBook-Pro.local>
    58	andrey-sysoev <andrey.sysoev@stud.hshl.de>
    30	Amer195 <163016879+Amer195@users.noreply.github.com>
    34	SamRB-dev <sadimrahmanbadhon@gmail.com>

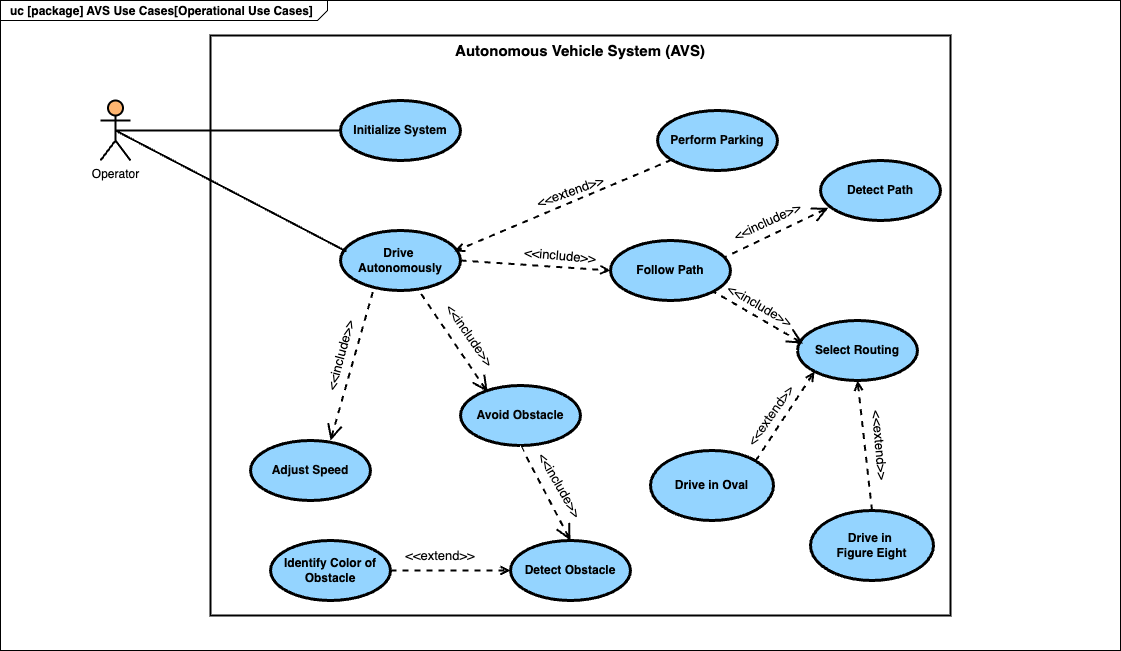
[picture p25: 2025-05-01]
Report/UseCaseDiagram.png

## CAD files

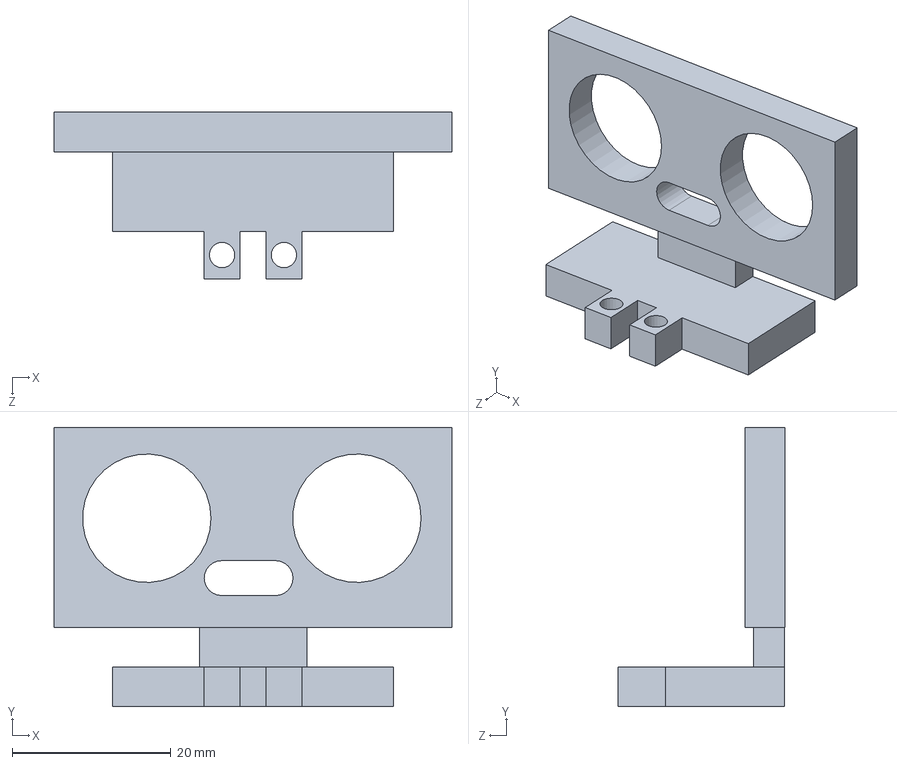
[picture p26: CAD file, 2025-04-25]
Mechanical Prototype Design/SolidWorks Parts/Ultrasonic Sensor Mount.SLDPRT
50.2 x 35.2 x 21.0 mm

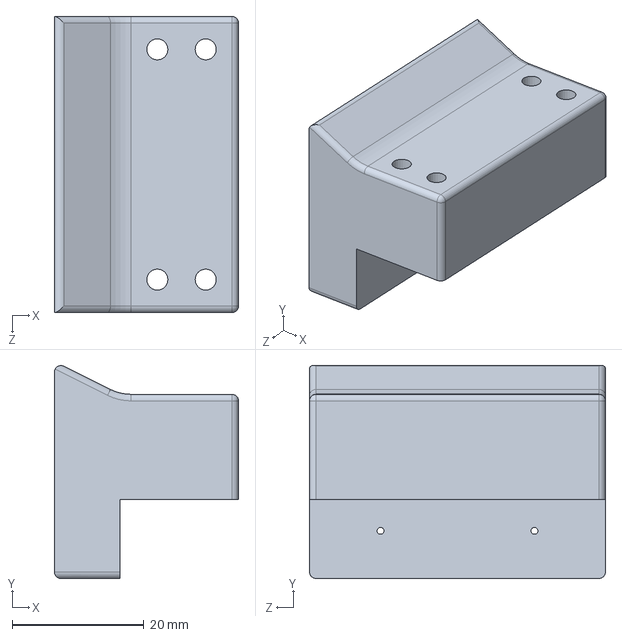
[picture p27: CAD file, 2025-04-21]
Mechanical Prototype Design/SolidWorks Parts/Motor Mount.SLDPRT
28.0 x 32.4 x 45.0 mm

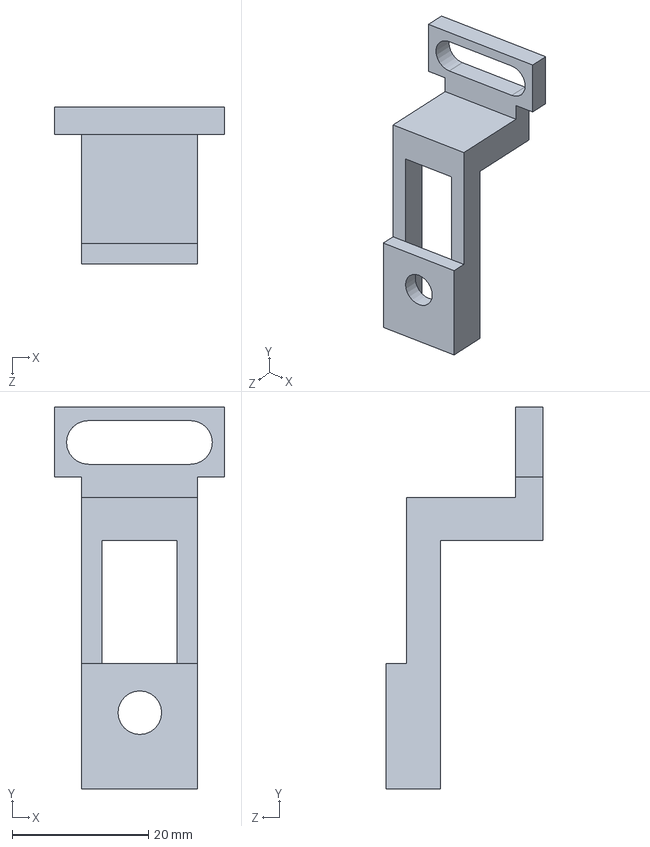
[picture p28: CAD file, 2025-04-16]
Mechanical Prototype Design/SolidWorks Parts/IR Sensor Mount.SLDPRT
25.0 x 56.1 x 23.0 mm

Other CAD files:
Mechanical Prototype Design/SolidWorks Parts/Battery Mount.sldprt
Mechanical Prototype Design/STL files/Battery Mount.stl
Mechanical Prototype Design/STL files/IR Sensor Mount.STL
Mechanical Prototype Design/STL files/Motor Mount.STL
Mechanical Prototype Design/STL files/Ultrasonic Sensor Mount.STL

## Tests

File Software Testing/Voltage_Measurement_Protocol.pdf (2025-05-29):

1

Voltage Measurement Protocol for Autonomous Vehicle Critical Components

Toos: Multimeter for accurate voltage measurements.

Measurement Specifications

1. L298N H-Bridge Motor Driver

Measured Voltage: 10.98V
Operating Voltage Range: 5V to 35V
Note: The L298N motor driver operates reliably within this voltage range.
2. HC-SR04 Ultrasonic Sensor

Measured Voltage: 4.98V
Operating Voltage: 5V
Note: The sensor can operate reliably within 4.5V to 5.5V voltage range.
3. KY-003 IR Sensor

Measured Voltage: 4.63V
Operating Voltage Range: 3.3V to 5V
Note: The sensor operates correctly within this voltage range.

Measurement Procedure

1. Preparation:

Ensure the robot is powered off.
Inspect all connections for any visible damage or loose wires and switch. Turn on the robot's power supply.
2. Voltage Measurement:

L298N H-Bridge:

Set the multimeter to DC voltage mode.
Place the black probe on the ground (GND) terminal.
Place the red probe on the motor supply voltage input terminal. Record the voltage reading.

HC-SR04 Ultrasonic Sensor:

Place the black probe on the GND pin. Place the red probe on the VCC pin. Record the voltage reading.

KY-003 IR Sensor:

Place the black probe on the GND pin. Place the red probe on the VCC pin. Record the voltage reading.

2

Documentation And Analysis

Date | Component | Measured
| | Voltage | Operating
| | | Range | Status | Notes
28/05/2025 | L298N H-Bridge
| Driver | 10.98V | 5V – 35V | OK | Within safe operating
| | | | | range
28/05/2025 | HC-SR04 Ultrasonic
| Sensor | 4.98V | 4.5V – 5.5V | OK | Within proper range
28/05/2025 | KY-003 IR Sensor | 4.63V | 3.3V – 24V | OK | Stable voltage supply

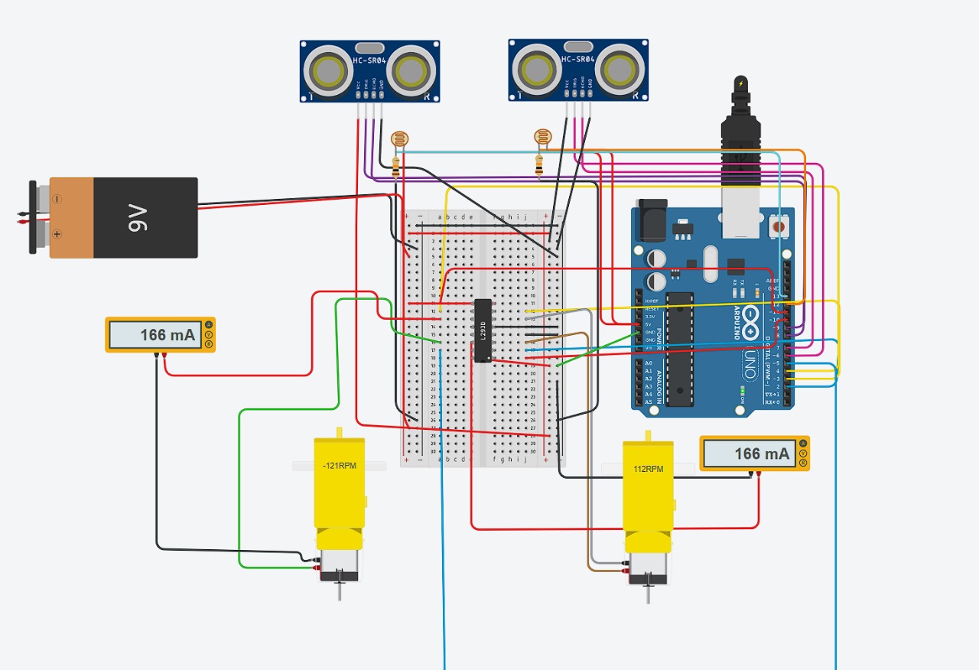
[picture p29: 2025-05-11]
CurrentAndVoltageMeasurements/MotorsCurrent.jpeg

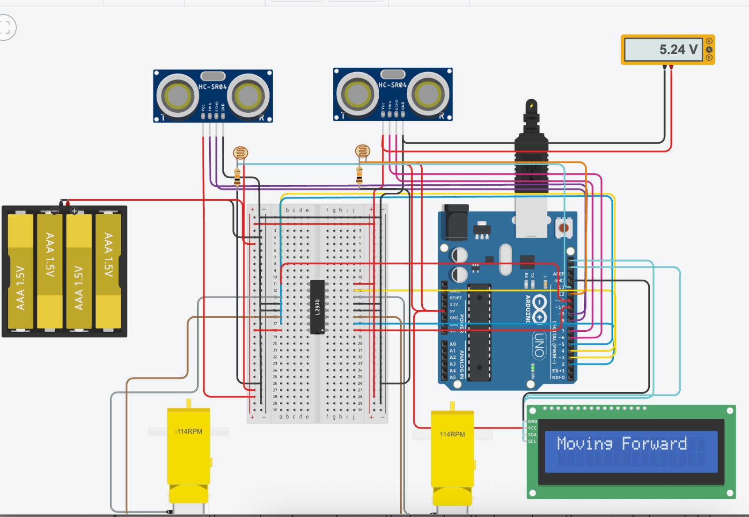
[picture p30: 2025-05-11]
CurrentAndVoltageMeasurements/UltrasonicSensorVoltage.jpeg

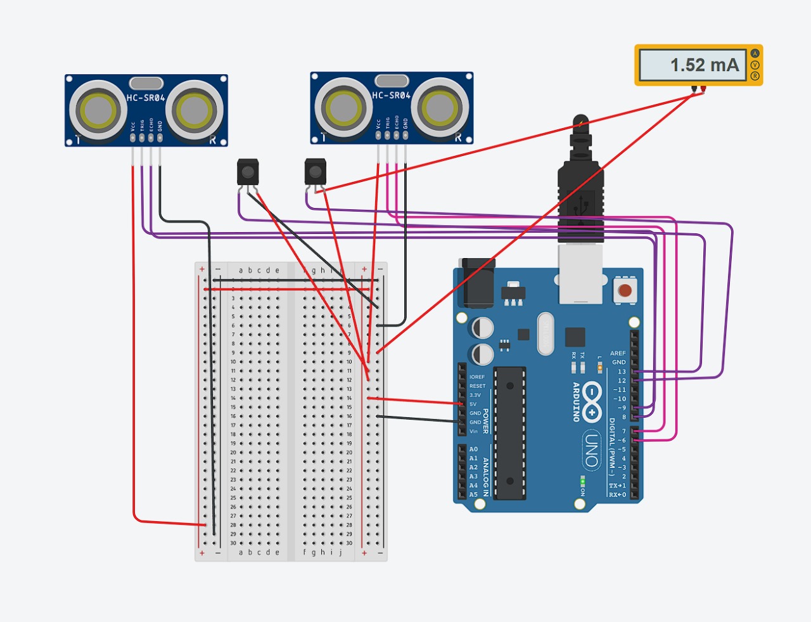
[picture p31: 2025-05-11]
CurrentAndVoltageMeasurements/IRSensorCurrent.jpeg

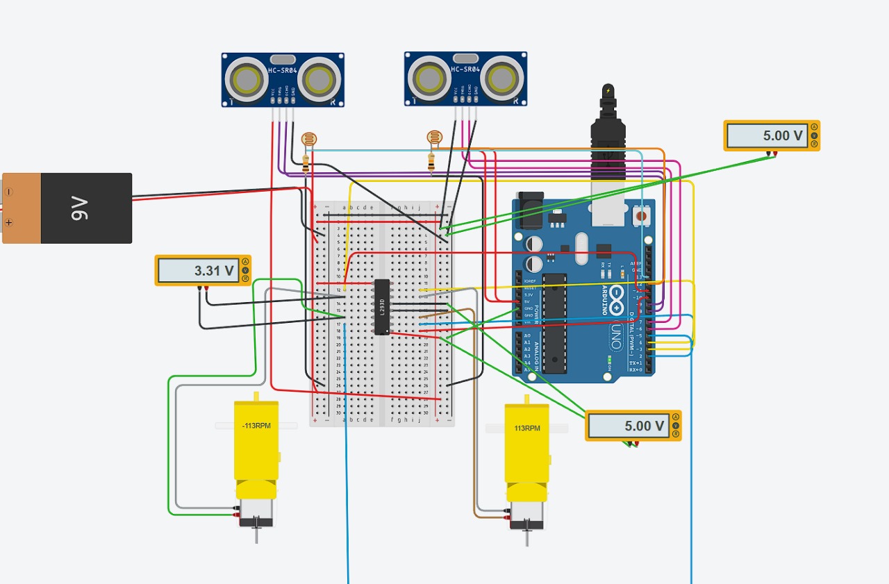
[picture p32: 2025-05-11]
CurrentAndVoltageMeasurements/MotorsVoltage.jpeg

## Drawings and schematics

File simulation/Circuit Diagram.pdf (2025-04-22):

A

1 | 2 | 3 | 4 | 5 | 6

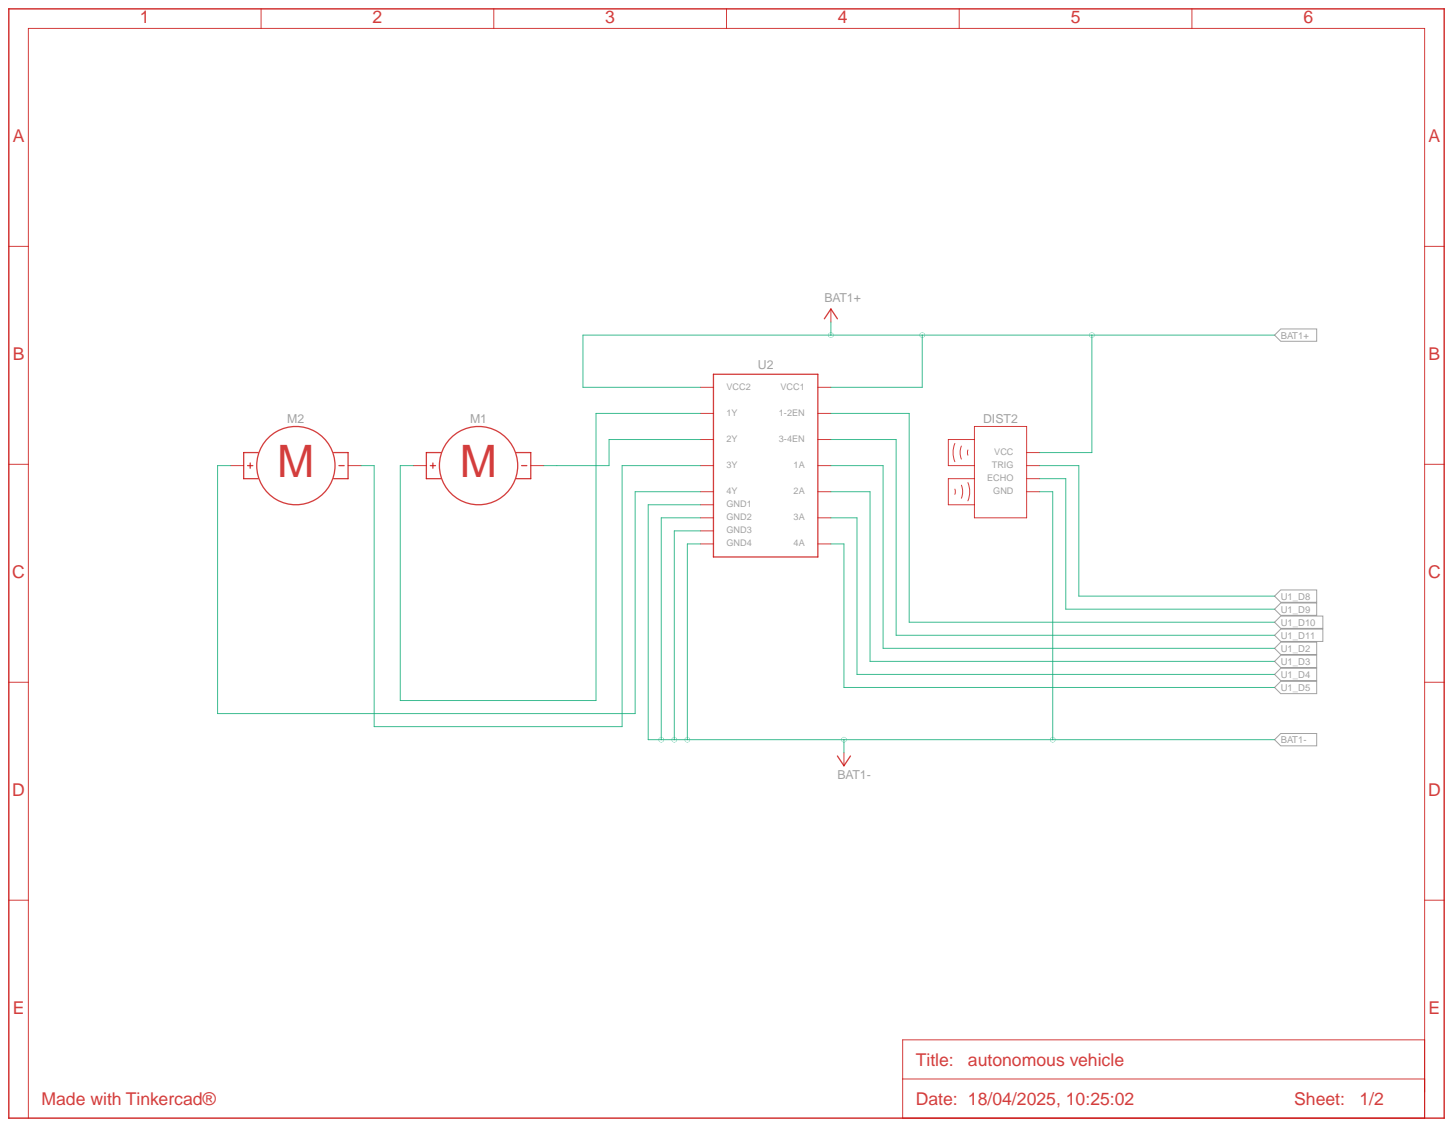
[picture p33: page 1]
Date: 18/04/2025, 10:25:02; Sheet: 1/2; GND1 GND2; VCC2; VCC1; GND3 GND4; VCC TRIG; GND; ECHO; DIST2; BAT1+; BAT1-

Title: autonomous vehicle

Made with Tinkercad®

A

1 | 2 | 3 | 4 | 5 | 6

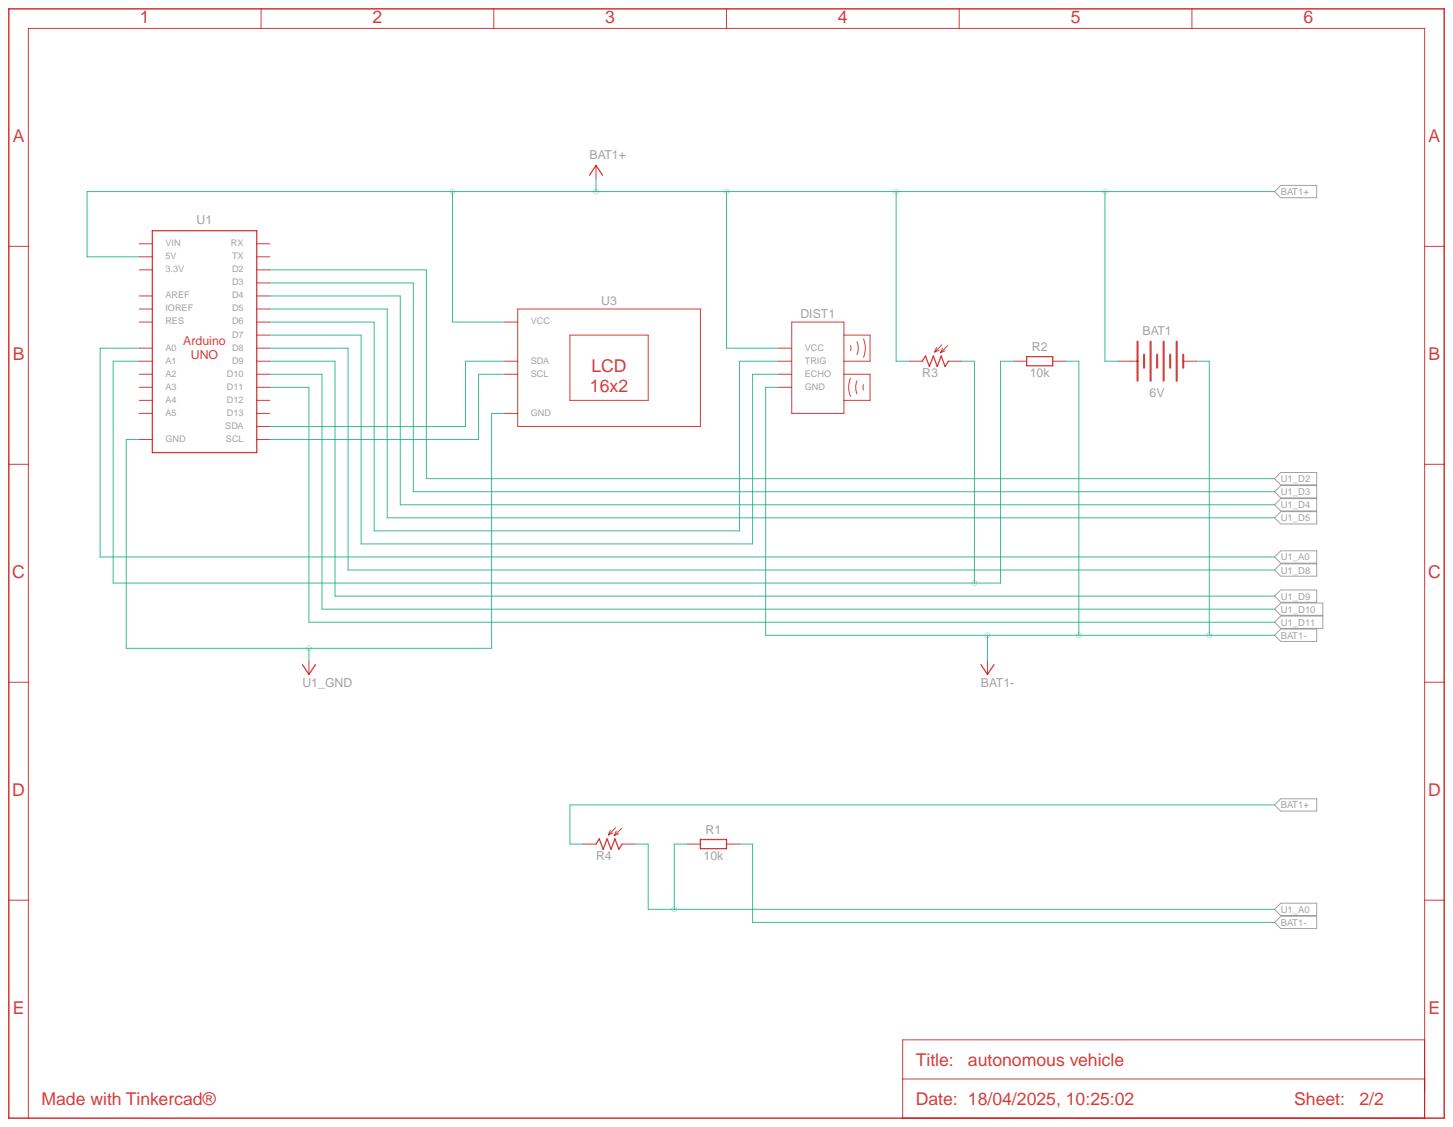
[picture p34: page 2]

BAT1+

VCC GND

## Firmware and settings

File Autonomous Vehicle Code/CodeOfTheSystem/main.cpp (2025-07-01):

#include <Arduino.h>
#include "MotorControl.h"
#include "UltrasonicSensor.h"
#include "RobotNavigation.h"

// Create hardware instances
MotorControl motor;
UltrasonicSensor rightUltrasonic(RIGHT_TRIG_PIN, RIGHT_ECHO_PIN);
UltrasonicSensor leftUltrasonic(LEFT_TRIG_PIN, LEFT_ECHO_PIN);
RobotNavigation robotNav(&rightUltrasonic, &leftUltrasonic, &motor);

// Arduino initialization
void setup() {
  // Setup motor pins as outputs
  pinMode(LEFT_MOTOR_SPEED_PIN, OUTPUT);
  pinMode(RIGHT_MOTOR_SPEED_PIN, OUTPUT);
  pinMode(LEFT_MOTOR_FORWARD_PIN, OUTPUT);
  pinMode(LEFT_MOTOR_BACKWARD_PIN, OUTPUT);
  pinMode(RIGHT_MOTOR_FORWARD_PIN, OUTPUT);
  pinMode(RIGHT_MOTOR_BACKWARD_PIN, OUTPUT);

  // Initialize ultrasonic sensors
  rightUltrasonic.begin();
  leftUltrasonic.begin();

  // Start navigation system
  robotNav.begin();
}

// Arduino main loop
void loop() {
  
  robotNav.updateNavigation();   // Execute robot logic
}

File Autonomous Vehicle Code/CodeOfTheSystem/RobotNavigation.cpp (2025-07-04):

#include "RobotNavigation.h"

// Constructor: Assign passed sensor and motor objects
RobotNavigation::RobotNavigation(UltrasonicSensor* right, UltrasonicSensor* left, MotorControl* motorControl, ColorSensor* red) {
  rightSensor = right;
  leftSensor = left;
  motor = motorControl;
  red = red;
}

void RobotNavigation::begin() {
  pinMode(LINE_SENSOR_LEFT, INPUT);
  pinMode(LINE_SENSOR_RIGHT, INPUT);
}

// Change robot's state and act accordingly
void RobotNavigation::setRobotState(int state) {
  currentState = state;

  // Execute behavior for each state
  switch (currentState) {

    case OBSTACLE_AVOID:
      obstacleStep = 0;
      handleObstacleAvoidance(); // Begin obstacle avoidance
      break;

    case LEFT:
      while (digitalRead(LINE_SENSOR_RIGHT) == LOW)
          motor->turnLeft(DefaultTurnSpeed); //Turn left until the right IR sensor detects the line
      motor->stopMotors();
      break;

    case RIGHT:
      while (digitalRead(LINE_SENSOR_LEFT) == LOW)
          motor->turnRight(DefaultTurnSpeed); // Turn right until the left IR sensor detects the line
      motor->stopMotors();
      break;

    case LINE_SEARCH:
      handleLineSearch(); // Begin line search
      break;
  }
}

// Main logic loop: process line and obstacle sensors
void RobotNavigation::updateNavigation() {

  // Read line sensors
  int leftLine = digitalRead(LINE_SENSOR_LEFT);
  int rightLine = digitalRead(LINE_SENSOR_RIGHT);

  // Read obstacle sensors
  float rightDistance = rightSensor->getDistance();
  float leftDistance = leftSensor->getDistance();

  // Choose action based on sensor readings
  if (((rightDistance < maxDistance && rightDistance > minDistance) ||
      (leftDistance < maxDistance && leftDistance > minDistance)) &&
      !red->ColorSensorObserve()) {
    motor->stopMotors();
    delay(300);
    setRobotState(OBSTACLE_AVOID);  // Obstacle detected
  }
  if (leftLine == HIGH && rightLine == LOW) {
    motor->stopMotors();
    setRobotState(LEFT);  // Right sensor losts the line
  } else if (leftLine == LOW && rightLine == HIGH) {
    motor->stopMotors();
    setRobotState(RIGHT);  // Left sensor losts the line
  } else if (leftLine == LOW && rightLine == LOW) {
    if (currentState == LEFT) {
      motor->stopMotors();
      setRobotState(RIGHT);
    } else if (currentState == RIGHT) {
      motor->stopMotors();
      setRobotState(LEFT);
    }
  }
}

// Behavior for obstacle avoidance sequence
void RobotNavigation::handleObstacleAvoidance() {
  switch (obstacleStep) {
    // Step 0: Move backward to clear way for maneuver
    case 0:
      motor->stopMotors();
      delay(100);
      motor->moveBackward(DefaultBackwardSpeed);
      delay(200);
      obstacleStep++;
      break;
    // Step 1: Rotate left before bypass
    case 1:
      motor->rotateLeft(80);
      delay(600);
      motor->stopMotors();
      delay(1000);
      obstacleStep++;
      break;
  }
  // Check obstacle
  float rightDistance = rightSensor->getDistance();
  float leftDistance = leftSensor->getDistance();

  // Obstacle detected
  if ((rightDistance < 100 && rightDistance > 3) ||
      (leftDistance < 100 && leftDistance > 3)) {

    // Rotate back on the line to switch the direction on bypass
    motor->rotateRight(68);
    while (true) {
      bool leftLine = digitalRead(LINE_SENSOR_LEFT);
      bool rightLine = digitalRead(LINE_SENSOR_RIGHT);
      if (rightLine == HIGH) {
        motor->stopMotors();
        delay(500);
        break;
      }
    }
    // Bypass the obstacle
    motor->rotateRight(75);
    delay(500);
    motor->stopMotors();
    delay(700);
    motor->moveForward(75);
    delay(750);
    motor->stopMotors();
    delay(600);
    motor->rotateLeft(75);
    delay(650);
    motor->stopMotors();
    delay(700);
    motor->moveForward(75);
    delay(800);
    motor->stopMotors();
    delay(600);
    motor->turnLeft(75);
    delay(600);
    motor->stopMotors();
    delay(1000);
    currentState = LINE_SEARCH;
    setRobotState(LINE_SEARCH);

  } else {
    motor->rotateRight(75);
    delay(350);
    motor->stopMotors();
    delay(500);
    motor->moveForward(70);
    delay(900);
    motor->stopMotors();
    delay(1000);
    motor->rotateRight(70);
    delay(500);
    motor->stopMotors();
    delay(500);
    currentState = LINE_SEARCH;
    setRobotState(LINE_SEARCH);
  }
}

void RobotNavigation::handleLineSearch() {
  bool foundLine = false;
  unsigned long startTime = millis();
  while (millis() - startTime < searchTimeout) {
    motor->turnLeft(120);
    delay(110);
    motor->stopMotors();
    delay(100);
    bool leftLine = digitalRead(LINE_SENSOR_LEFT);
    bool rightLine = digitalRead(LINE_SENSOR_RIGHT);
    if (leftLine == HIGH || rightLine == HIGH) {
      motor->stopMotors();
      delay(100);
      leftLine = digitalRead(LINE_SENSOR_LEFT);
      rightLine = digitalRead(LINE_SENSOR_RIGHT);
      if (leftLine == HIGH)
        while (rightLine == HIGH)
            motor->turnLeft(DefaultTurnSpeed);
      if (rightLine == HIGH)
        while (leftLine == HIGH)
            motor->turnRight(DefaultTurnSpeed);
      motor->stopMotors();
      delay(100);
      motor->moveForward(DefaultForwardSpeed);
      delay(100);
      foundLine = true;
      break;
      return;
    }

    motor->turnRight(DefaultTurnSpeed);
    delay(100);
    motor->stopMotors();
    delay(100);
    leftLine = digitalRead(LINE_SENSOR_LEFT);
    rightLine = digitalRead(LINE_SENSOR_RIGHT);
    if (leftLine == HIGH || rightLine == HIGH) {
      motor->stopMotors();
      delay(100);
      if (leftLine == HIGH)
        while (leftLine == HIGH) motor->turnRight(DefaultTurnSpeed);
      if (rightLine == HIGH)
        while (rightLine == HIGH) motor->turnLeft(DefaultTurnSpeed);
      motor->stopMotors();
      delay(100);
      motor->moveForward(DefaultForwardSpeed);
      delay(100);
      foundLine = true;
      break;
    }
  }
}

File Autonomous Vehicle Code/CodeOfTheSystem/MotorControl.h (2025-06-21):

#ifndef MOTORCONTROL_H
#define MOTORCONTROL_H

#include <Arduino.h>

// Motor control pin definitions
#define LEFT_MOTOR_SPEED_PIN 10       // PWM pin controlling left motor speed
#define RIGHT_MOTOR_SPEED_PIN 11      // PWM pin controlling right motor speed

#define LEFT_MOTOR_FORWARD_PIN 2      // Digital pin to move left motor forward
#define LEFT_MOTOR_BACKWARD_PIN 3     // Digital pin to move left motor backward
#define RIGHT_MOTOR_FORWARD_PIN 4     // Digital pin to move right motor forward
#define RIGHT_MOTOR_BACKWARD_PIN 5    // Digital pin to move right motor backward

class MotorControl {
  public:
    void moveForward(int speed);       // Move robot forward
    void moveBackward(int speed);      // Move robot backward
    void turnLeft(int speed);          // Turn robot left
    void turnRight(int speed);         // Turn robot right
    void rotateLeft(int speed);        // Rotate robot left
    void rotateRight(int speed);       // Rotate robot right
    void stopMotors();                 // Stop both motors
};

#endif

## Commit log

2025-04-14 adding initial version of the HW part - battery holder
    [breadboard_battery_holder.SLDPRT]
2025-04-16 Changing models.
    [Holder RS Sensor left.SLDPRT]
2025-04-16 Adding models
    [Rs holder.SLDPRT, motor tire holder left.SLDPRT, motor tire holder right.SLDPRT]
2025-04-16 Ultrasonic Bracket WIP
    [Box.SLDASM, Part1.SLDPRT, Part2.SLDPRT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]
2025-04-17 Problem with right holder, didn't save change. Uploading saved version.
    [motor tire holder right.SLDPRT]
2025-04-17 Adding full assembly
    To open requires all new holders+new moters and battery
2025-04-18 Ultrasonic Sensor Mount for servo motor
    [Box.SLDASM, Part1.SLDPRT, Part2.SLDPRT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]
2025-04-18 sg90 servo holder
    [sg90_servo_holder.SLDASM, sg90_servo_holder.SLDPRT, sg90_servo_holder_screw_area.SLDPRT]
2025-04-18 Final Design Proposals
    [Ultrasonic_Holder_For_Servo_Motor(Final).SLDASM, Ultrasonic_Holder_For_Servo_Motor.SLDASM, sg90_servo_holder(Final).SLDASM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]
2025-04-19 Final Design
    [Rs holder.SLDPRT, Ultrasonic_Holder_For_Servo_Motor(Final).SLDASM, Ultrasonic_bracket.SLDPRT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]
2025-04-19 Final Design v.2.0
    [Ultrasonic_bracket.SLDPRT, sg90_servo_holder.SLDPRT]
2025-04-21 Servo Holder, Small changes
    [sg90_servo_holder.SLDPRT]
2025-04-21 ultrasonic bracket changes
    [Ultrasonic_bracket.SLDPRT]
2025-04-21 ultrasonic update
    [Ultrasonic_bracket.SLDPRT]
2025-04-21 ultrasonic sensor
    [Ultrasonic_bracket.SLDPRT]
2025-04-21 Final Update
    [Ultrasonic_bracket changed.SLDPRT, Ultrasonic_bracket_with_holder final.SLDPRT]
2025-04-21 added final version of breadboard/battery holder and deleted the old one
    [Battery_holder_team_B2.stl, Updated_holder_battery.sldprt, breadboard_battery_holder.SLDPRT]
2025-04-27 final version of the battery holder
    [Updated_holder_battery.stl]
2025-04-27 moved .stl file to STL folder
    [Updated_holder_battery.stl]
2025-04-27 renamed .stl file for submission
    [Updated_holder_battery.stl]
2025-04-27 added some corretions in the code, use case diagram and readme file with a link on simulation
2025-04-27 replacing corrupted file
    [Battery_holder_team_B2.stl]
2025-04-27 restructured the code, implemented millis() instead of delay(100), added speed adjusting dependion on the states
2025-04-27 sorted folders
    [Ultrasonic_bracket changed.SLDPRT, Ultrasonic_bracket.SLDPRT, Ultrasonic_bracket_with_holder final.SLDPRT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]
2025-04-28 Reorganization of the GitRepositery
    Renamed Files with proper namings to illustrate content, Restructered and created Folders to make the Repositery easier to navigate
    [Battery Mount.sldprt, Battery Mount.stl, IR Sensor Mount.SLDPRT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]
2025-04-28 Add initial ToDo list for project tasks
    [ToDoList.xlsx]
2025-04-30 Added the first trial for arduino code deployment
    Changed the sensors that were used to imitate IR sensors to the real IR sensors behavior.
    made a slight change in the ultrasonic calculation value to make the maximum range at 200cm. (needs testing)
    made a slight change to the calculation of the distance to get more accurate results
    checked the entire code and compiled it.
    Next Steps: Test it in the Real Environment and adjust it as necessary .
2025-05-01 Optimized and corrected the IR sensor Code
    The sensor used turned out to be active LOW sensor so optimization in code was done accordingly.
    added needed sensor initialization with a HIGH signal to enable the internal pull up resistor
    [ArduinoCodeForDeployment.ino]
2025-05-01 Added a folder to contain the arduino code
    For cloning easily, A folder with the same name of the arduino sketch was added to facilitate opening of the ardiuno code with arduino IDE on PC
2025-05-01 Implimentance logic for obstacle avoidance. Updated current state machine with implimentation obstical avoidance. Implementation of timeout in obstacle avoidance.
    [AutonomousVehicleCode.cpp]
2025-05-01 New ToDoList
    [ToDoList.xlsx]
2025-05-03 Updated ToDo List
    [ToDoList.xlsx]
2025-05-04 updated ToDoList
    [ToDoList.xlsx]
2025-05-10 Adjusted the IR sensor Code
    used Digital representaion for the IR sensor due to the usage of digital IR instead of Analog. The code was adjusted to an Active LOW IR sensor.
2025-05-11 Adding current and voltage measurements of components
2025-05-11 Adjusted configuration for IR sensor pins
2025-05-19 corrected obstacle conditions due to timeouts
    [RobotNavigation.cpp]
2025-05-19 changed pins of line sensors and corrected values for ultrasonic
    [RobotNavigation.h]
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2025-05-25 Refactor README files across multiple directories to enhance structure and clarity; add detailed overviews and file listings.
    [ToDoList.xlsx]
2025-05-26 adding the last code version with corrected values for ultrasonic sensors and pins for IR sensor after teting these components on 19/05/2025
    [MotorControl.cpp, MotorControl.h, RobotNavigation.cpp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]
2025-05-26 adding a datasheet for the color sensor
2025-05-29 adding voltage measurement protocol, all unit tests placed in a separate folder
2025-05-29 adding log file with output values of US and IR sensors
2025-06-03 Update README.md to include details on current and voltage measurement and unit testing directories
2025-06-03 Fix typos and formatting in Current and Voltage Measurement section of README.md
2025-06-05 simple unit test for motors (to calibrate and test straight moving within hardware right/left assyncronization)
2025-06-06 XML for System simulation in UPPAAL (currently without OBSTACLE_AVOID state logic)
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2025-06-06 log file after testing motors and sensors on 06.06.2025
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2025-06-15 Test Color Sensor with mototor, IR and Ultrasonic sensors
2025-06-15 Motor, IR, Ultrasonic unit test with updated line search logic
2025-06-16 Added latest test with obstacle avoidance integration
    [MotorIRUltrasonic_UnitTest_UpdatedSearchLogic.ino, Motor_IR_Ultrasonic_Unit_Test.ino, Ultrasonic_IR_Motors_withObstacleAvoidance_Unit_Test.ino]
2025-06-20 Initial version of the final presentation with the textual content and some pictures
    [ToDoList.xlsx]
2025-06-20 Added the final version for IR, Ultrasonic, and motors with obstacle avoidance integration
    [ColorSensor_Unit_Test.ino, Ultrasonic_IR_Motors_withObstacleAvoidance_Unit_Test.ino]
2025-06-21 updated ToDoList.xlsx
    [ToDoList.xlsx]
2025-06-22 corrected some misspellings in cofigurations
    [AutonomousVehicleCode.cpp]
2025-06-22 corrected some syntax errors and misspellings
    [RobotNavigation.cpp, RobotNavigation.h]
2025-06-22 final updates in the codeand StateMachineDiagram, some corrections in presentatiom
    [ColorSensor.cpp, ColorSensor.h, RobotNavigation.cpp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]
2025-07-01 Add Initialization of Sensors and Actuators in Software implementation part, updated some styling in the latex report
2025-07-04 updated software implementation part and corrected misspellings in comments
    [RobotNavigation.cpp]
2025-07-06 Added the git contributions file
    [Battery Mount.sldprt]
